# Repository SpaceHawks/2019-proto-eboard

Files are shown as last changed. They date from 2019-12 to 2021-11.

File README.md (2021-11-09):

This repository contains the schematic and PCB for the 2019-2020 electrical board. For a walkthrough of this season's progress and an in-depth explanation of the system, see the IPRO report. For a quick glance at the schematic or boards, look in the [PDFs](/PDFs) folder. For information not printed on the schematic (e.g. datasheet links, trace widths), open the files in KiCad.

To view or edit these files, use KiCad version 5. You may need to [install the latest libraries](http://kicad.org/libraries/download/) if they don't come with your installation.

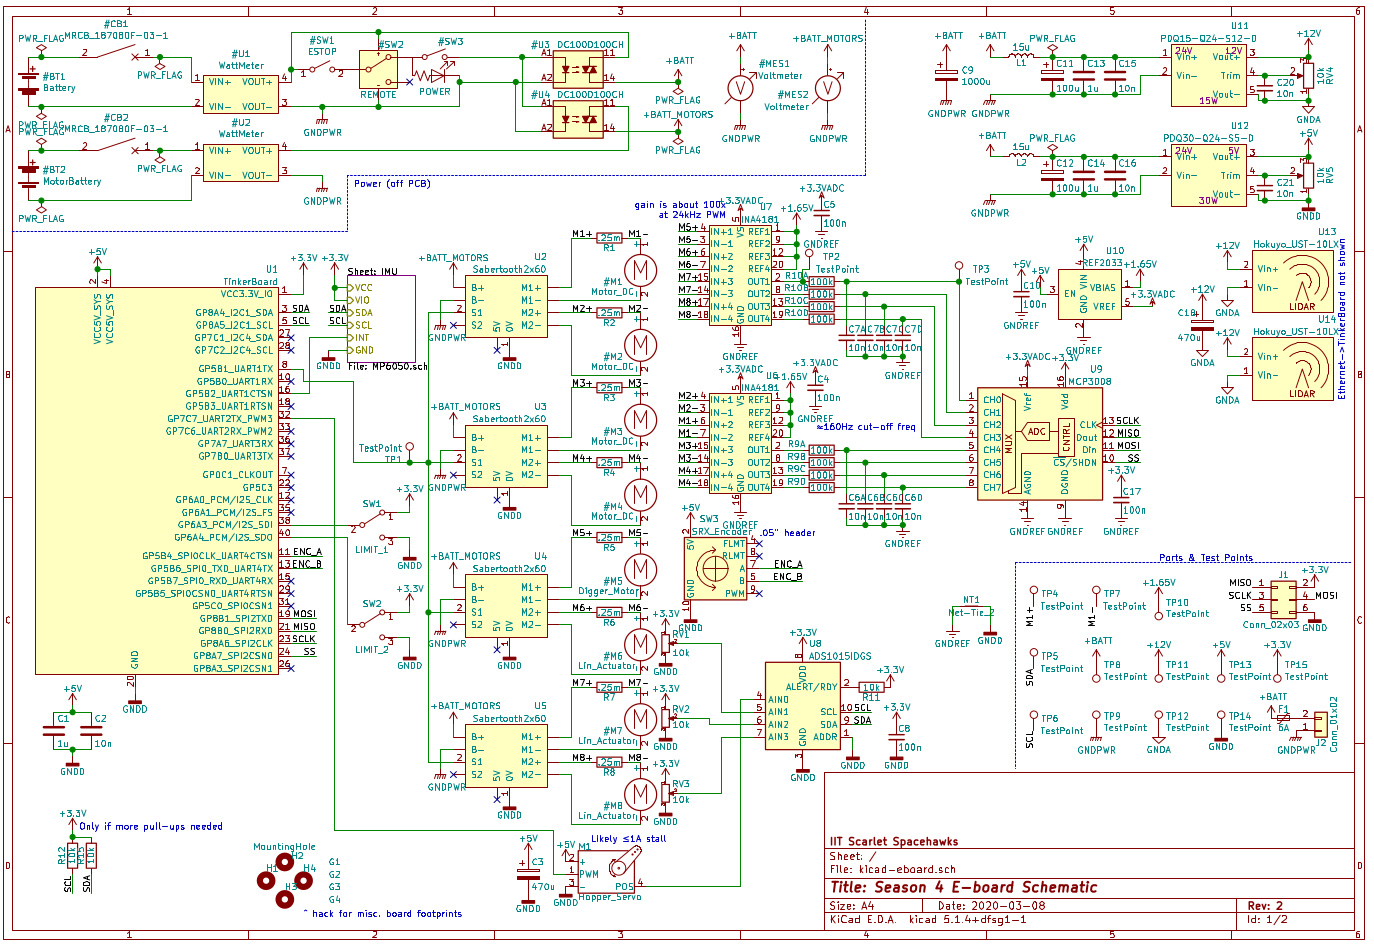
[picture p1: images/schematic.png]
Page 1 of the schematic (pretty much everything). See PDFs folder for something easier to read. The main schematic


# Spring 2020: Electrical Team IPRO Report

Gabriel Krell

Gregory Bonnema

Jack Pio

## I. Electrical Team Goals

The NASA RMC at Illinois Tech electrical team's goal was a reliable, professional electrical system for our robot. To accomplish this, we needed to plan the system in a reasonable, realistic way, implement our plan with well-reviewed eCAD, and turn those schematics into a physical robot. This year the team wanted to keep the same topology as previous years, making incremental changes. We aimed to have capable microelectronics and robot control systems running on top of a safe and reliable power system. Our robot would need to adhere to minimum specifications set by the competition (e.g. “The robot should include an emergency stop”) and those set by our goal-planning activity (e.g. “The robot should move”). We also had a nonfunctional goal: to spend as little as reasonably possible, designing to reuse parts from last year and use new parts we had already had. Overall our aim was to continue the success of the past NASA RMC teams, while improving efficiency and overall performance, making it easier to work together with the other subteams.

## II. Power Electronics

Conceptually, we split the electrical design of the robot into two sections. The “power electronics” section was chiefly concerned with getting power from batteries to motors in a safe way.

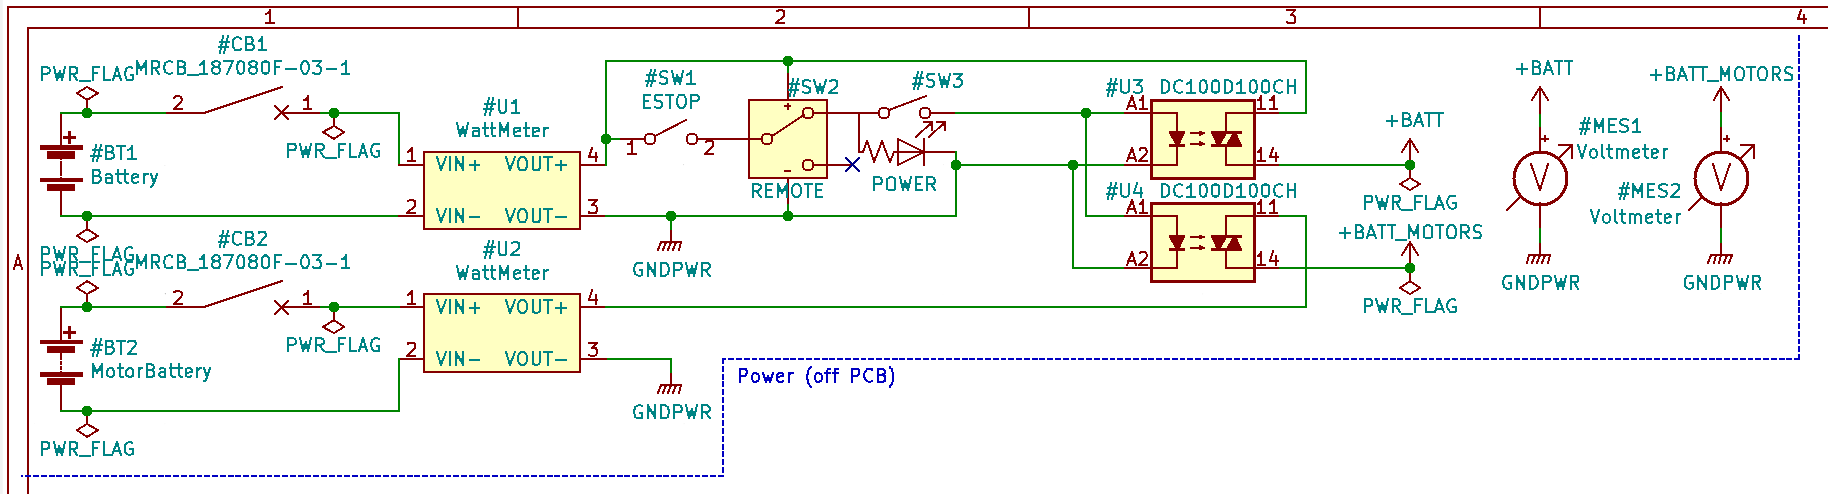
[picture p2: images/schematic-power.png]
The top-left corner of the schematic, labeled "Power (off PCB)" The power section of our final circuit schematic


### A. Initial Design

To lay out our plan for the power electronics section (and eventually make our final schematic), we started from a base of the previous year’s layout. Like other robotics competitions, the rules required an easy-to-reach emergency stop button (“E-stop”). We were also required to measure and display the total power consumed by the robot. On top of these mandatory elements, the relevant section of last year’s robot included:

- A single 3S hobby LiPo battery to power the robot

- A resettable circuit breaker to protect against sustained overcurrent

- A “remote E-stop” (actually a remote-controlled relay unit)

- A smaller, light-up power switch

- A solid-state relay (SSR) to toggle power to the robot

- Sabertooth 2x60 motor controllers to actually move the motors

- A panel-mount battery voltage display

We thought that this layout was simple to implement and was reasonably safe. We were able to build it using only parts that we already possessed from last year’s competition. However, we were concerned that the circuit breaker would take too long to open (10-25 seconds) during a projected overcurrent condition or short circuit. We investigated several options for faster responses: active control with a MOSFET, fast-blow fuses, and different circuit breakers. Unfortunately, breakers or fuses with our desired response characteristics were prohibitively expensive, and our subteam didn’t have the resources to implement active current protection. Ultimately, we compromised by including additional protection for the delicate microelectronics and trusting in the builtin current limiting on individual Sabertooths. Of course, we want to prevent any possible damage to the robot, but since this system includes a working E-stop and does not pose a fire hazard, it meets the relevant safety requirements.

### B. Modifications

We assembled a prototype electrical board as a proof-of-concept and began testing. We found that when motors were stalled, the high current draw would result in significant voltage drops across wires and especially across the SSR. This lowered the available voltage to below that required by the 12V-5V DC-DC converter, resulting in brownouts. We added a second SSR so that the microelectronics would not be affected by the high voltage drop across the SSR. We soon realized, however, that the high current was also causing the battery’s voltage to sag to unacceptable levels. To fix the problem, we added a second battery that would not be responsible for providing high current to the motors. This is not a perfect solution, because it required additional parts and weight, but it would perform well with the supplies on hand.

### C. Motor control

Like last year, we used Sabertooth 2x60 motor controllers. Each channel can supply up to 60A continuous or 120A peak; the Sabertooths are controlled via analog input, an R/C receiver, or serial input. Unfortunately, the controllers return no information about motor output or power consumption. To implement closed-loop control, we added output sensing for all motors: circuits to read the built-in potentiometers on the linear actuators, current sensing resistors on all motors, and a rotary encoder on the most critical motor.

## III. Microelectronics

The second section of the robot’s electronics system was responsible for sensor inputs, computation, and output signals. From the outset, we planned to use a PCB for reliable functionality in a small form factor.

The robot would be run by a single-board computer (SBC). The SBC would sense the outside world through an IMU and two LIDAR sensors, monitor the robot with current and position sensors, and output commands to the motor controllers. We initially used an ASUS Tinker Board, which we exchanged for a more powerful Raspberry Pi 3B+ at the request of the Programming Department.

### A. IMU

We included an inertial measurement unit (IMU) that would report the robot’s velocity and position in space. Because we already had a breakout board from Sparkfun, and because good libraries are available for it, we chose the MPU-6050 for our IMU. The MPU-6050 communicates with the SBC via I2C, a relatively slow multi-device protocol which is easy to connect and route on a circuit board. Sparkfun publishes schematics and board files for their hardware, so we included both the MPU-6050 circuit and headers to connect to the breakout. This way, we could use the expensive breakout board in our first PCB, but use the bare chip if a second version of the PCB forced us to order components.

### B. Potentiometer ADC

The robot incorporates three linear actuators and a four-wire servo to move the regolith collection system and sense how much icy regolith has been collected. All three linear actuators and the servo have built-in potentiometers for position sensing. Because our SBC was not able to read analog inputs by itself, we included an ADC to measure these voltages. We chose the ADS1015, an inexpensive 12-bit ADC that connects to the same I2C bus already used for the IMU. Adafruit sells an ADS1015 breakout board commonly used as an ADC for Raspberry Pis, so the Programming team would enjoy easy-to-use libraries to interface with the chip. Throughout the component selection process, we worked closely with Programming to make sure they would have drivers and libraries to interface with the hardware we chose.

### C. Current Sensing

After struggling with brownouts caused by excessive power consumption by the motors, we became concerned with monitoring motor current. The competition scoring penalized high power usage, but not enough for points to be our motivation. Rather, we wanted the robot to be able to detect when a motor was stalled (high current) or disconnected (no current despite a command to move). This would allow us to prevent system instability caused by current spikes, to improve navigation with this extra information about the robot’s movement, and to increase our eventual competition score.

We measured the voltage across very small (.25mΩ) shunt resistors to calculate the current going through each motor. Two leads from each resistor went to a differential current sense amplifier, which amplified the small bipolar voltage difference into a unipolar voltage high enough to be accurately measured by a fast ADC.

This was probably the most technically difficult part of the project. As the motors spin forwards or backwards, the motor controllers output 12V/0V or 0V/12V on the two leads (referenced to the negative lead of the battery). This means that a shunt resistor on either side will sometimes be at 12V potential, so a “high-side” current measurement system is necessary. Typical ADCs are damaged by inputs higher than their supply voltage (usually 3.3V or 5V), so we had to use a specialized IC to make a high-side differential measurement.

We also needed to amplify this measurement. To avoid large power losses in the resistors, we needed to keep the voltage drop across them as low as possible. To limit resistor consumption to 1W at the max motor current of 60A, we could only allow a voltage drop of 15mV. An ADC’s resolution is evenly distributed over its entire input range, so a 12-bit 3.3V ADC would only have 18 values to choose from to represent current of 0-60A. Amplifying this value before it went into the ADC allowed us to have more precise current measurements.

Finally, we needed to filter the amplified output of the differential measurement. The Sabertooth 2x60 modulates motor power with PWM at 24kHz. The ADC we chose had a maximum sample rate of 75k sps across all 8 channels, well below the Nyquist rate of the signal. Even if we were using a faster ADC, we didn’t want our software to process 384,000 samples per second, which would consume valuable system resources. Instead, we used an RC filter with a cut-off frequency of around 160Hz. This would smooth high-frequency PWM while giving us an accurate picture of changes in motor current. We considered using a Butterworth-response Sallen-Key filter, which has a much sharper cutoff of high frequencies and is easy to implement. But because we needed eight of these filters in limited board space and budget, we went with the RC filter.

## IV. Implementation

Implementation of our design was split into three parts: schematic capture, PCB design, and physical layout of large parts on the robot. We used KiCad for all our eCAD, and tracked versions with GitHub so that everyone was able to see the most up-to-date files.

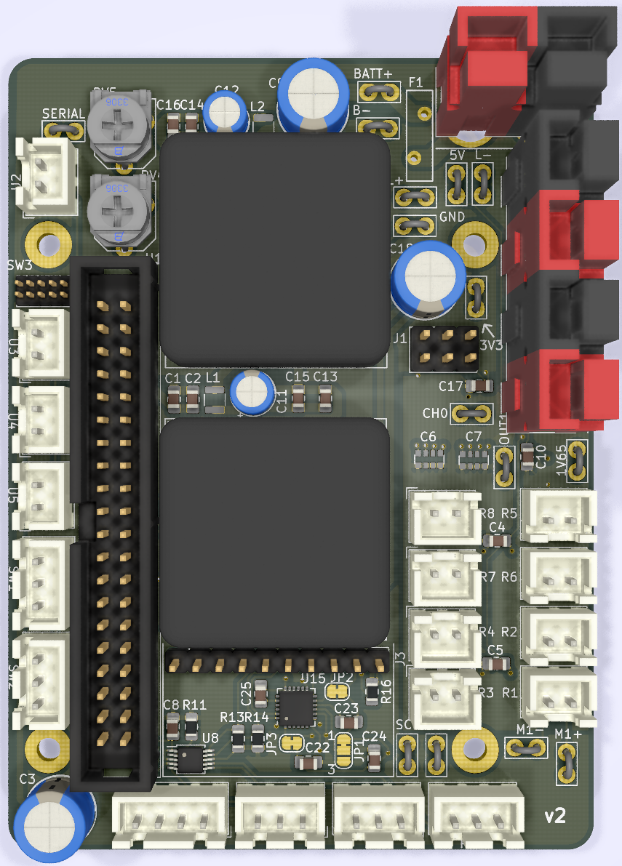
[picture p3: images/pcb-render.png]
A render of the final PCB
 The unpopulated PCB attached to a Tinker Board SBC

### A. Schematic

We began with a rough schematic focusing on the power electronics. We updated the schematic as we figured out how last year’s robot worked and made our own design changes. Having a reference design helped us quickly build the electrical system for a prototype robot, allowing us to verify the design and let Programming test out their code on real hardware. The prototype bot was invaluable for debugging the brownout problems mentioned in Section II-C. Work on the physical prototype and the schematic proceeded in tandem. Once we had implemented the microelectronics section on perfboard and verified motor control functionality, we were ready to design the PCB. At the same time, we knew that our well-tested power electronics section was unlikely to change, so we began planning the physical layout of the large parts on our robot.

### B. PCB

The PCB was designed over the course of several weeks, with an eye towards a small form factor and easy testability. To save space, we designed the board to stack on top of the SBC, and we included test points for the inevitable debugging sessions later on. After an initial online review, we ordered and tested the first version of the board. This version correctly supported motor control and the IMU, but we quickly realized that unlike the previous year’s Arduino, the Tinker Board does not have a built-in ADC. We had connected the built-in potentiometers of the linear actuators to GPIO pins that could only accept digital input. Luckily, we had scheduled plenty of time for a possible second PCB. We added the necessary ADC, along with some quality-of-life changes and the current sensing detailed in III-C, and ordered a second board.

### C. Physical Layout

With the designs of the PCB and schematic finalized, all that remained was the problem of how to apply these designs onto the robot itself. Given the extremely fine dust present in the competition, we decided to enclose the electrical system in a polycarbonate “e-box”. Our design was sealed with silicone caulk and included a removable front panel which slid on a set of rails. Although not entirely airtight, the box was designed to protect components from major dust contamination. We used weather-resistant panel-mount ports to connect the e-box with the motors, sensors, and emergency stop located elsewhere on the robot.

Our available space was scarcely larger than the total volume of the components, so we made careful mockups of different layouts to come up with a good arrangement. To save space, we stacked pairs of motor controllers, and stacked the PCB on top of the Tinker Board. The rest of the e-box was laid out around these core components, keeping in mind the aforementioned consideration for difficulty of wiring.

## VI. Conclusion

Although this year’s competition was interrupted by the COVID-19 pandemic, we still accomplished many of our goals for the robot and laid a strong foundation for next year. We also explored several promising areas for innovation in next year’s competition.

We designed and implemented a working, safe power system for the robot. We were able to identify historical trouble spots: the datasheet for the SSRs specified a large heat sink, and no heat sink had ever been used. This year, we used advanced phase change composite (PCC) heat sinks donated by AllCell, a local battery manufacturer. The lightweight phase change material absorbs energy as it melts, but is held together by a graphite substrate. This improves the performance and lifetime of the SSRs without adding a prohibitive amount of weight to the robot.

We are also proud of our microelectronics system. Rigorous online review and a schedule that allowed us time for a second spin produced a high-quality board. We were able to catch small issues: for instance, our second version of the board added rounded edges, optional pull-up resistors, and connectors that make it impossible to accidentally connect electrically-incompatible components. The removal of extraneous parts and overall simplification of the system allowed us to make a much more compact system than previous years.

We also accomplished our goal of minimal spending. Historically, the Electrical department has been responsible for a significant portion of the team’s budget. Last year, we spent $3,075 on parts and tools. This year, we spent $410, $232 of which went to soldering stations (the team possessed a single pencil-style iron with a damaged tip). Throughout the season, we designed with price in mind, using cheap or already-owned components.

As of this report, the pandemic has prevented us from receiving components to assemble the PCB, but we are hopeful that the parts will arrive so we can assemble the board and allow Programming to remotely test their software. We are confident in this year’s design, and hope it to be a great stepping stone to the future of the Scarlet Spacehawks.

## VII. Resources

[Don’t Fear the Filter: Lowpass Edition - Elliot Williams for Hackaday](https://hackaday.com/2017/03/08/dont-fear-the-filter-lowpass-edition/)

[Filter Design in Thirty Seconds - Bruce Carter for TI](http://www.ti.com/lit/an/sloa093/sloa093.pdf)

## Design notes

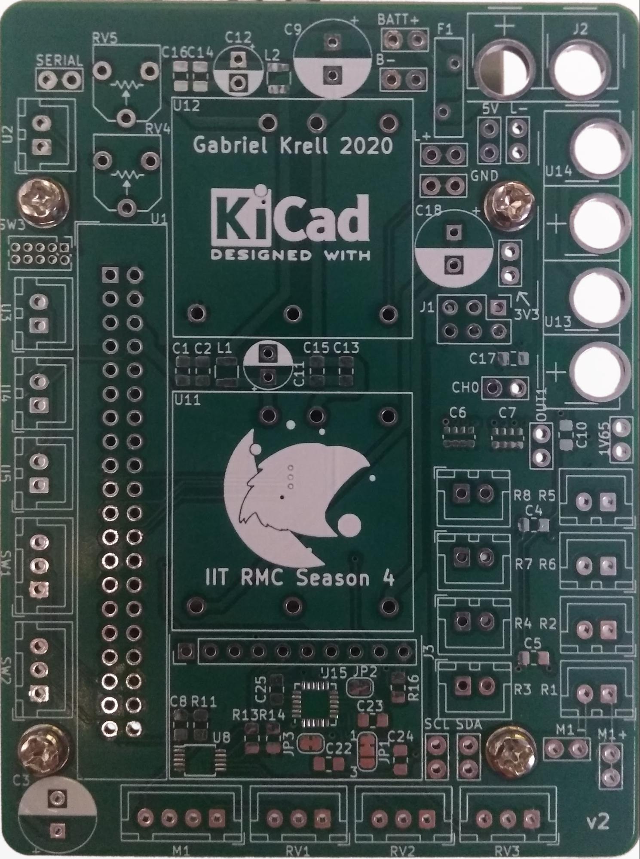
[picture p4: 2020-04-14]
images/pcb-unpopulated.jpg

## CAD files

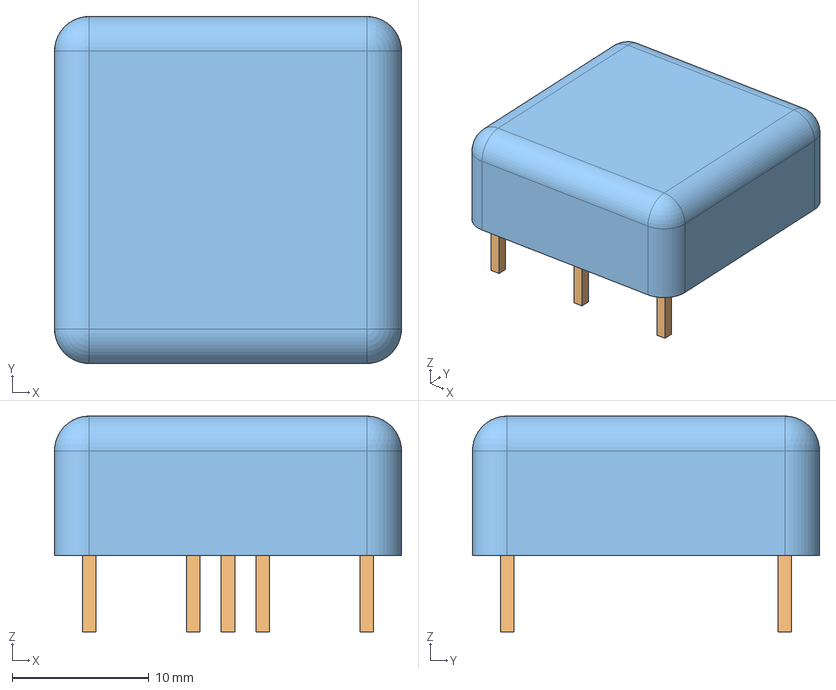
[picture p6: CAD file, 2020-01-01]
PDQ15.FCStd
25.4 x 25.4 x 15.8 mm
BottomPlastic
Pins
TopPlastic

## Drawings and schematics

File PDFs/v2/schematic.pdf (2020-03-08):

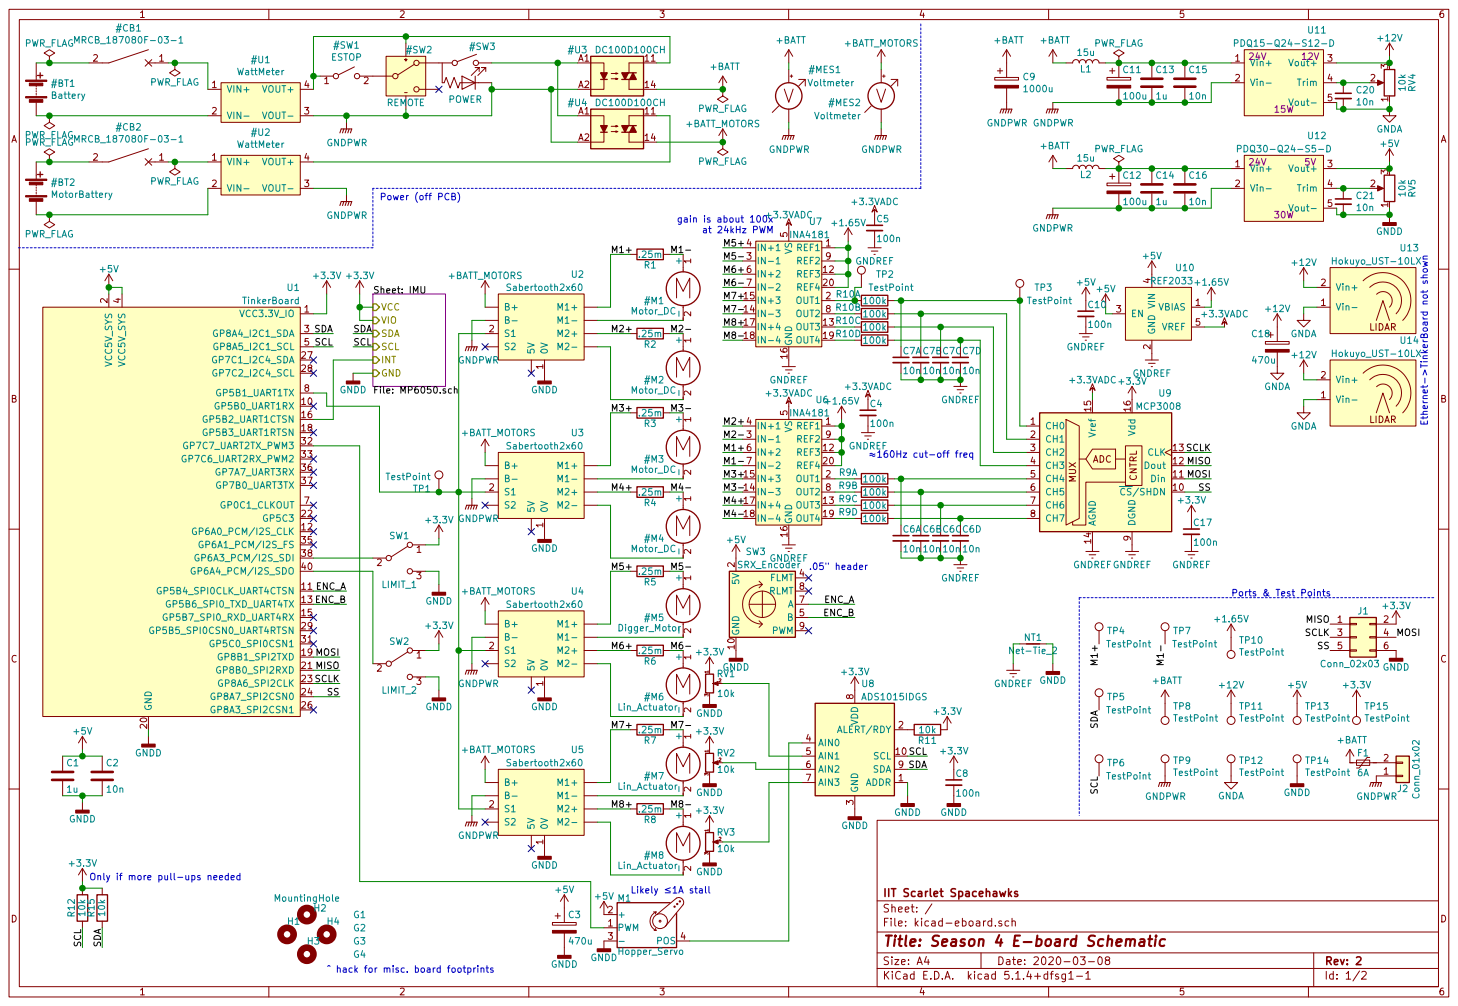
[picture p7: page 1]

Sheet: IMU
File: MP6050.sch VCC GND
VIO
INT SCL SDA

.05" header ^ hack for misc. board footprints

IIT Scarlet Spacehawks
File: kicad-eboard.sch Sheet: /
Id: 1/2 Title: Season 4 E-board Schematic

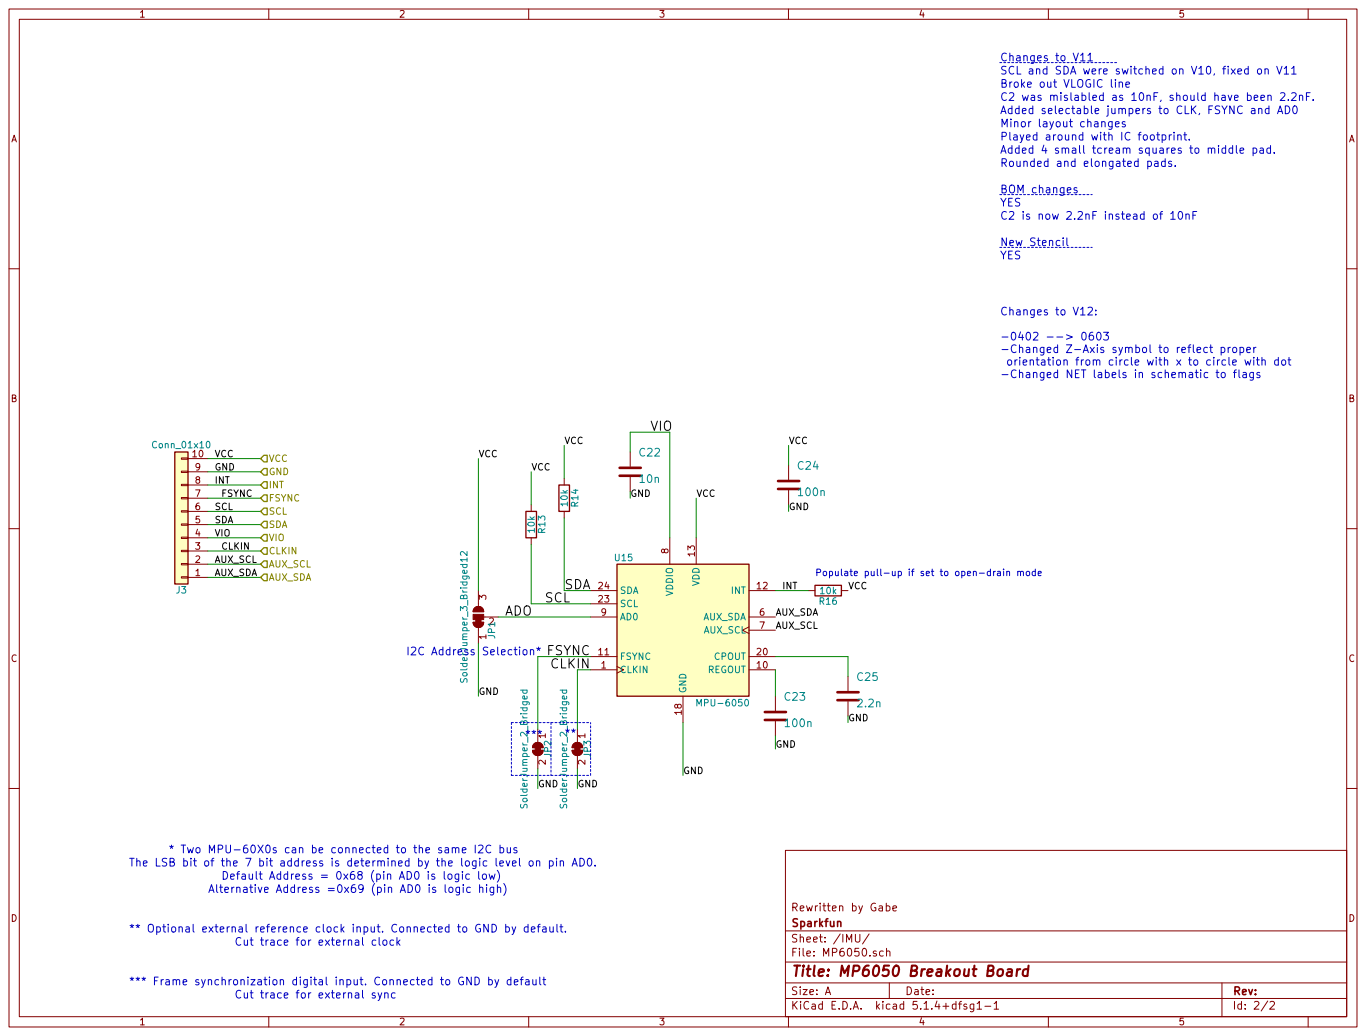
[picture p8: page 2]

Changes to V11
SCL and SDA were switched on V10, fixed on V11
C2 was mislabled as 10nF, should have been 2.2nF. Broke out VLOGIC line BOM changes

Added selectable jumpers to CLK, FSYNC and AD0
YES C2 is now 2.2nF instead of 10nF Minor layout changes
Played around with IC footprint.
Added 4 small tcream squares to middle pad.
Rounded and elongated pads.

-Changed Z-Axis symbol to reflect proper
orientation from circle with x to circle with dot -Changed NET labels in schematic to flags

Populate pull-up if set to open-drain mode

* Two MPU-60X0s can be connected to the same I2C bus

The LSB bit of the 7 bit address is determined by the logic level on pin AD0.

Alternative Address =0x69 (pin AD0 is logic high)

Rewritten by Gabe
File: MP6050.sch Sheet: /IMU/ Sparkfun

*** Frame synchronization digital input. Connected to GND by default

Id: 2/2 Title: MP6050 Breakout Board

Cut trace for external sync

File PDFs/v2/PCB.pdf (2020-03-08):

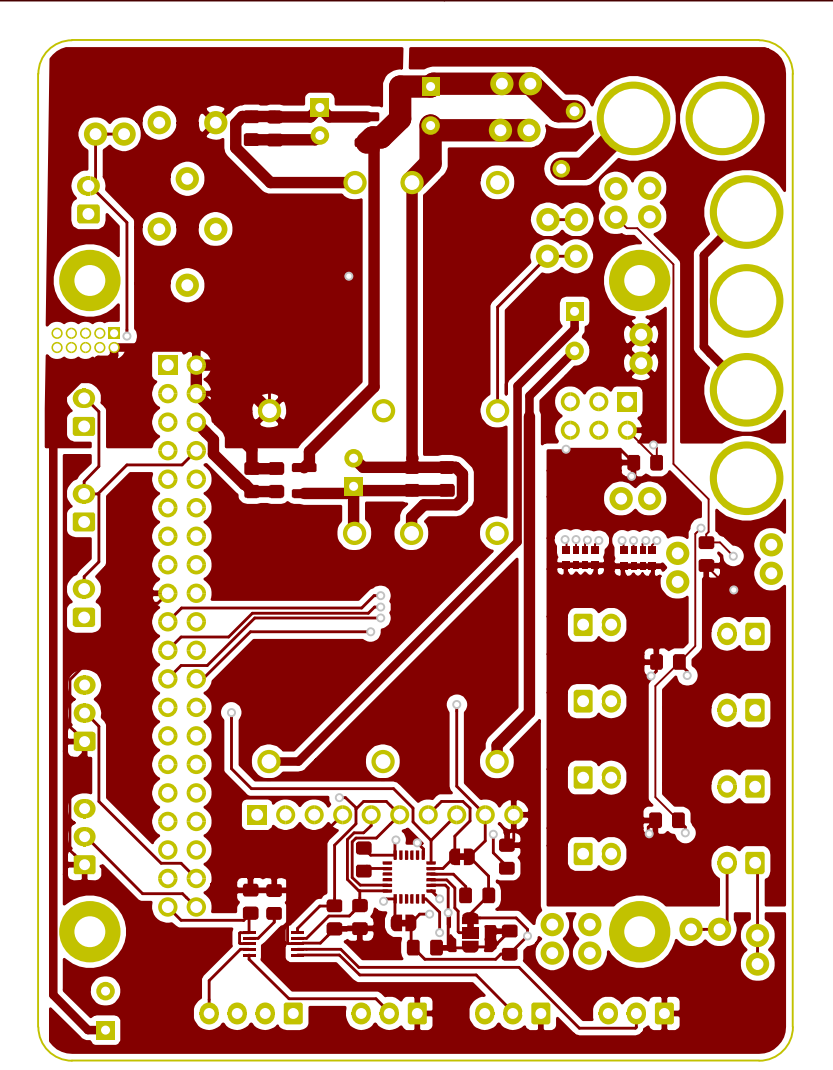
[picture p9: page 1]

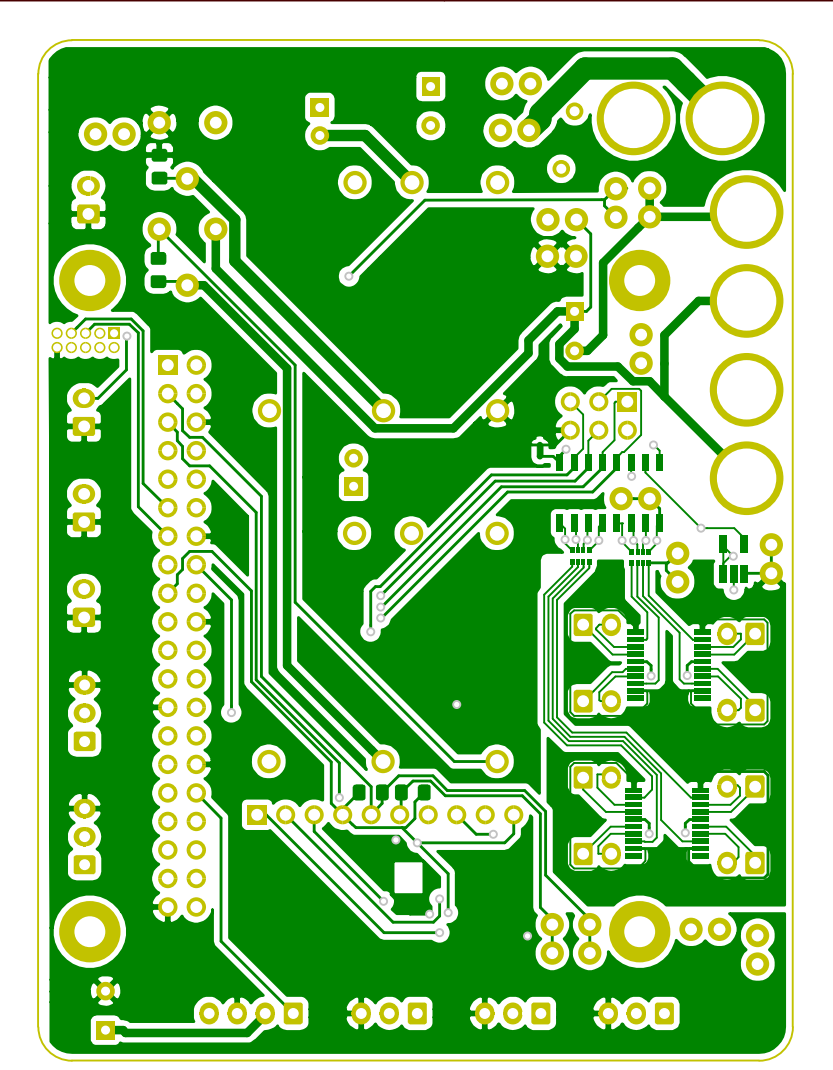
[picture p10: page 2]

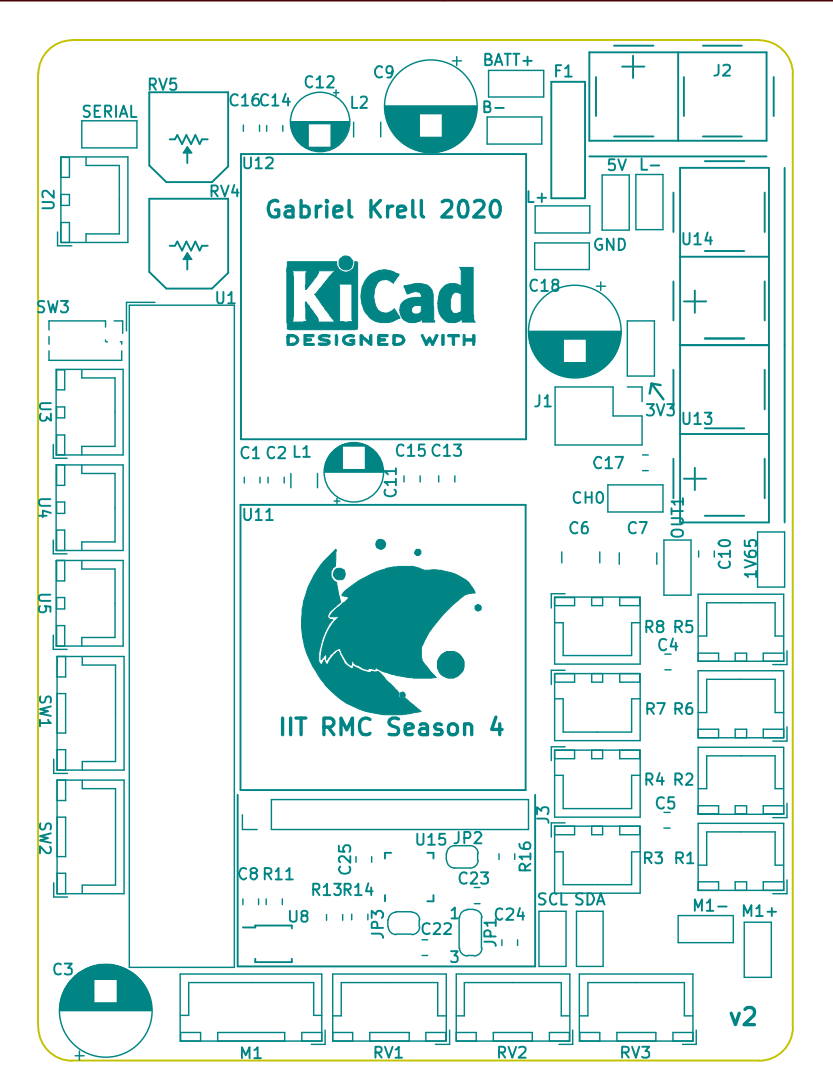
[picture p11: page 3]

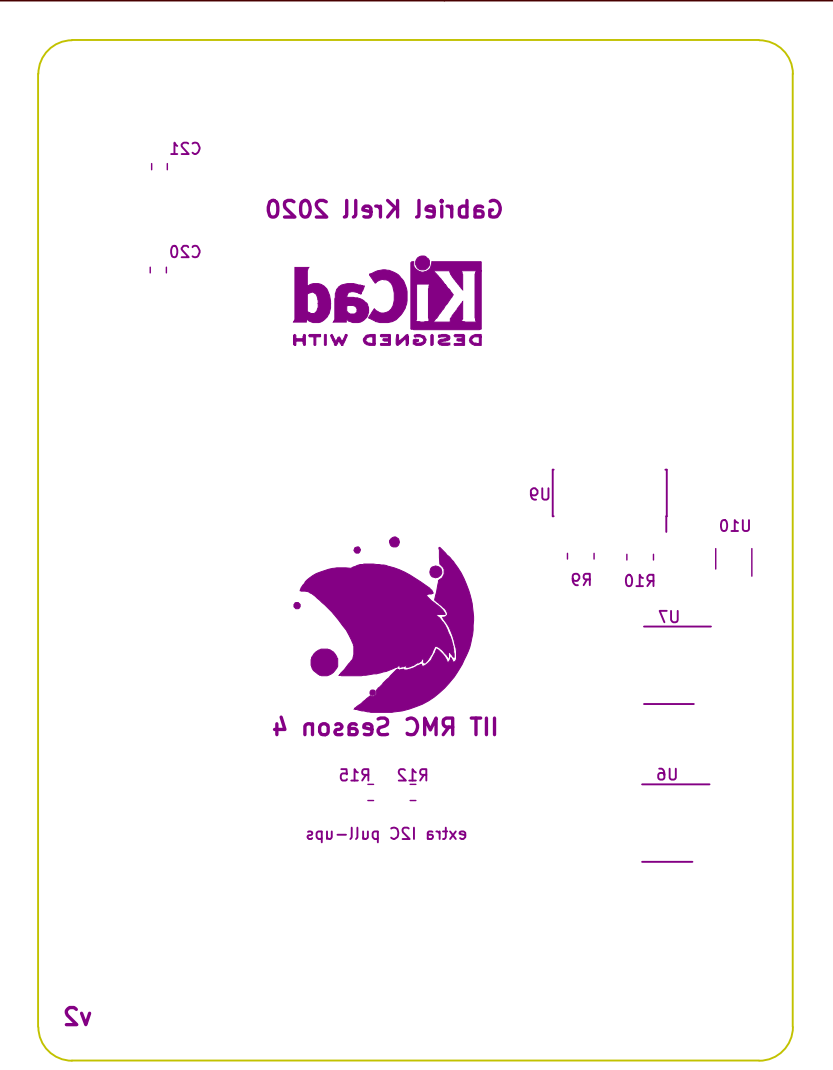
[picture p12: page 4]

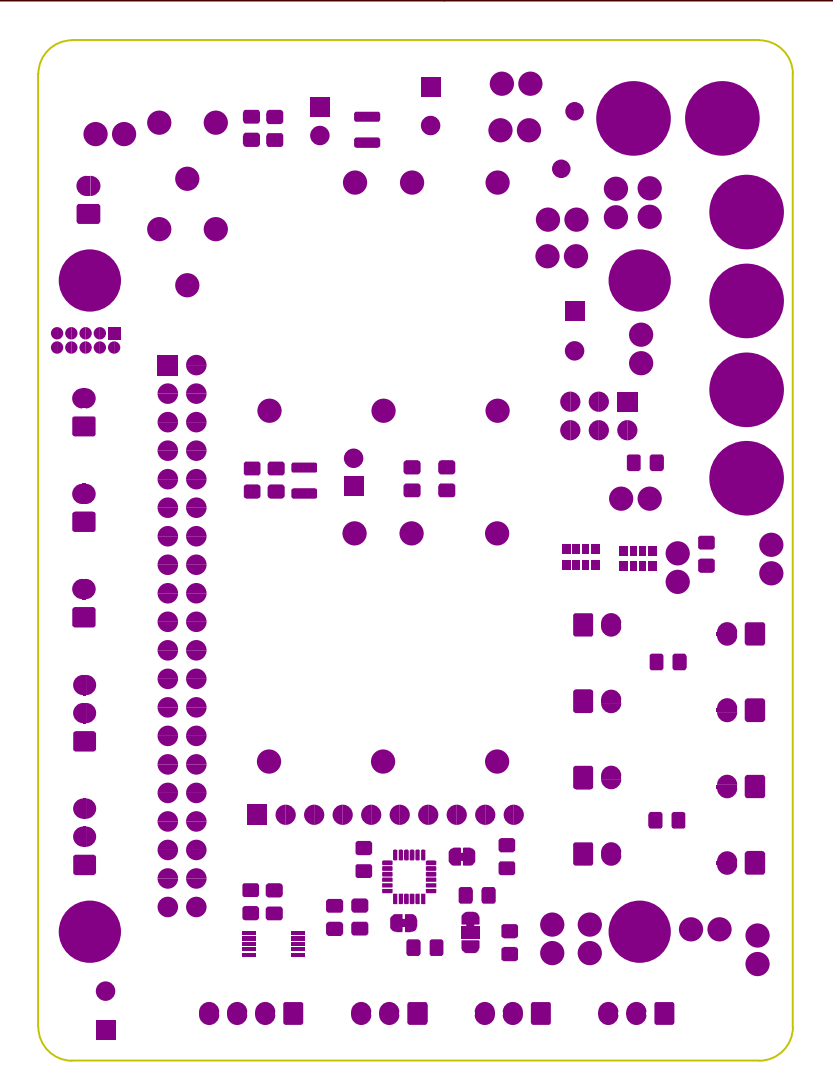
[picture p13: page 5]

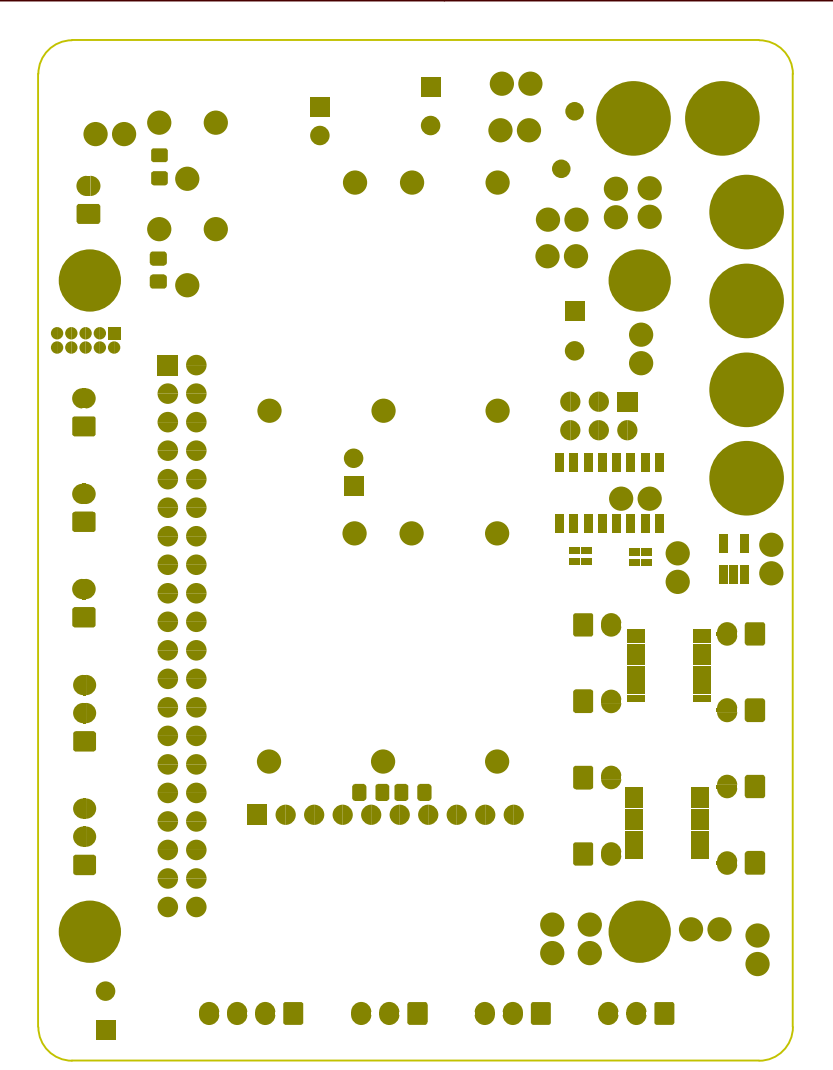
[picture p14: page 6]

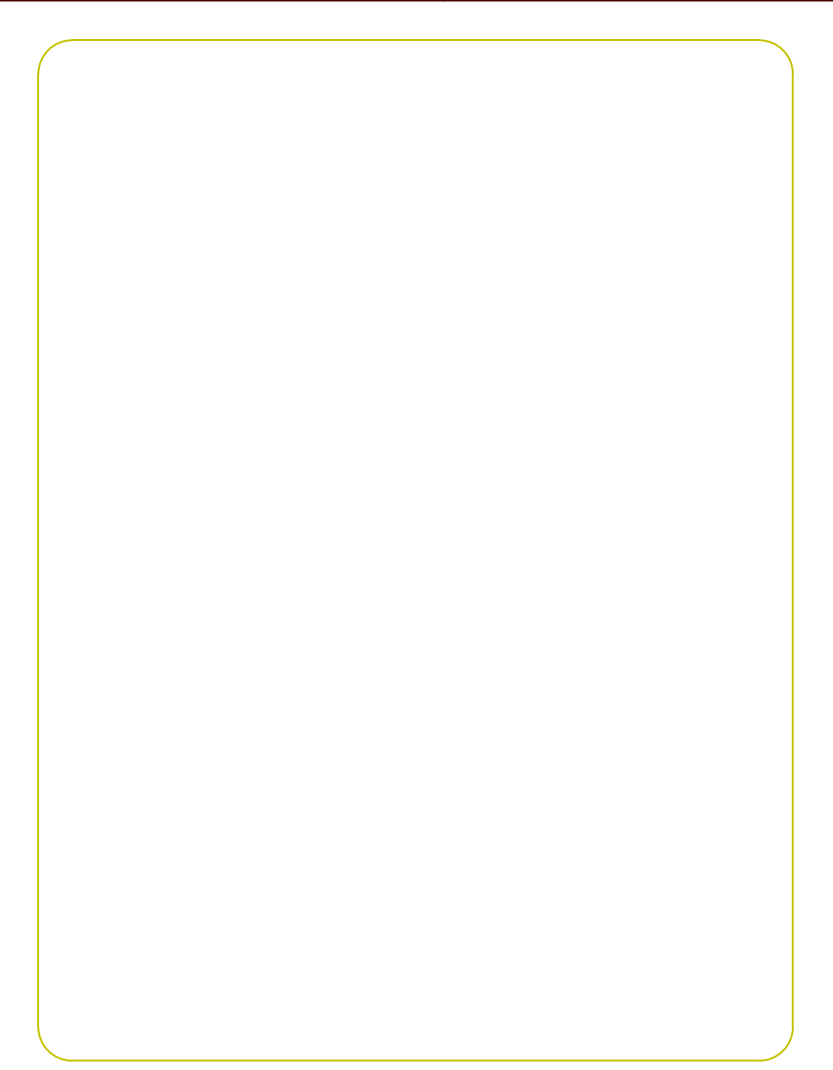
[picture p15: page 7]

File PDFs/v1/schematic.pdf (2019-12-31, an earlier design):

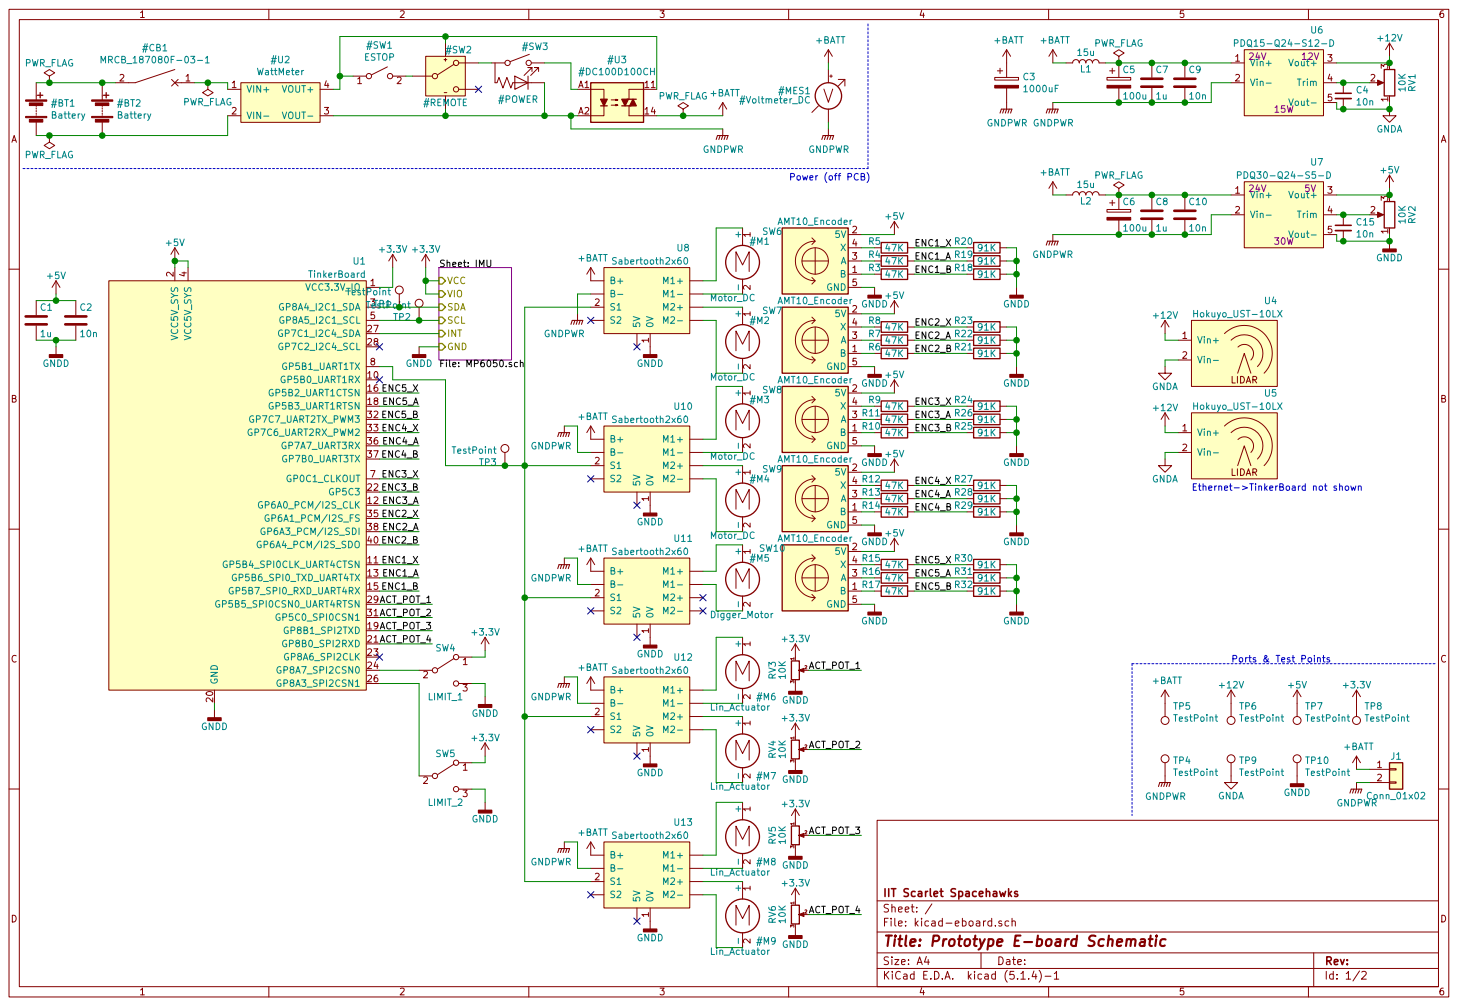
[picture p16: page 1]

Sheet: IMU
File: MP6050.sch VCC GND
VIO
INT SCL SDA

3 X | ENC2_A

1 | ENC2_B

3 X | ENC4_A

1 | ENC4_B

IIT Scarlet Spacehawks
File: kicad-eboard.sch Sheet: /
Id: 1/2 Title: Prototype E-board Schematic

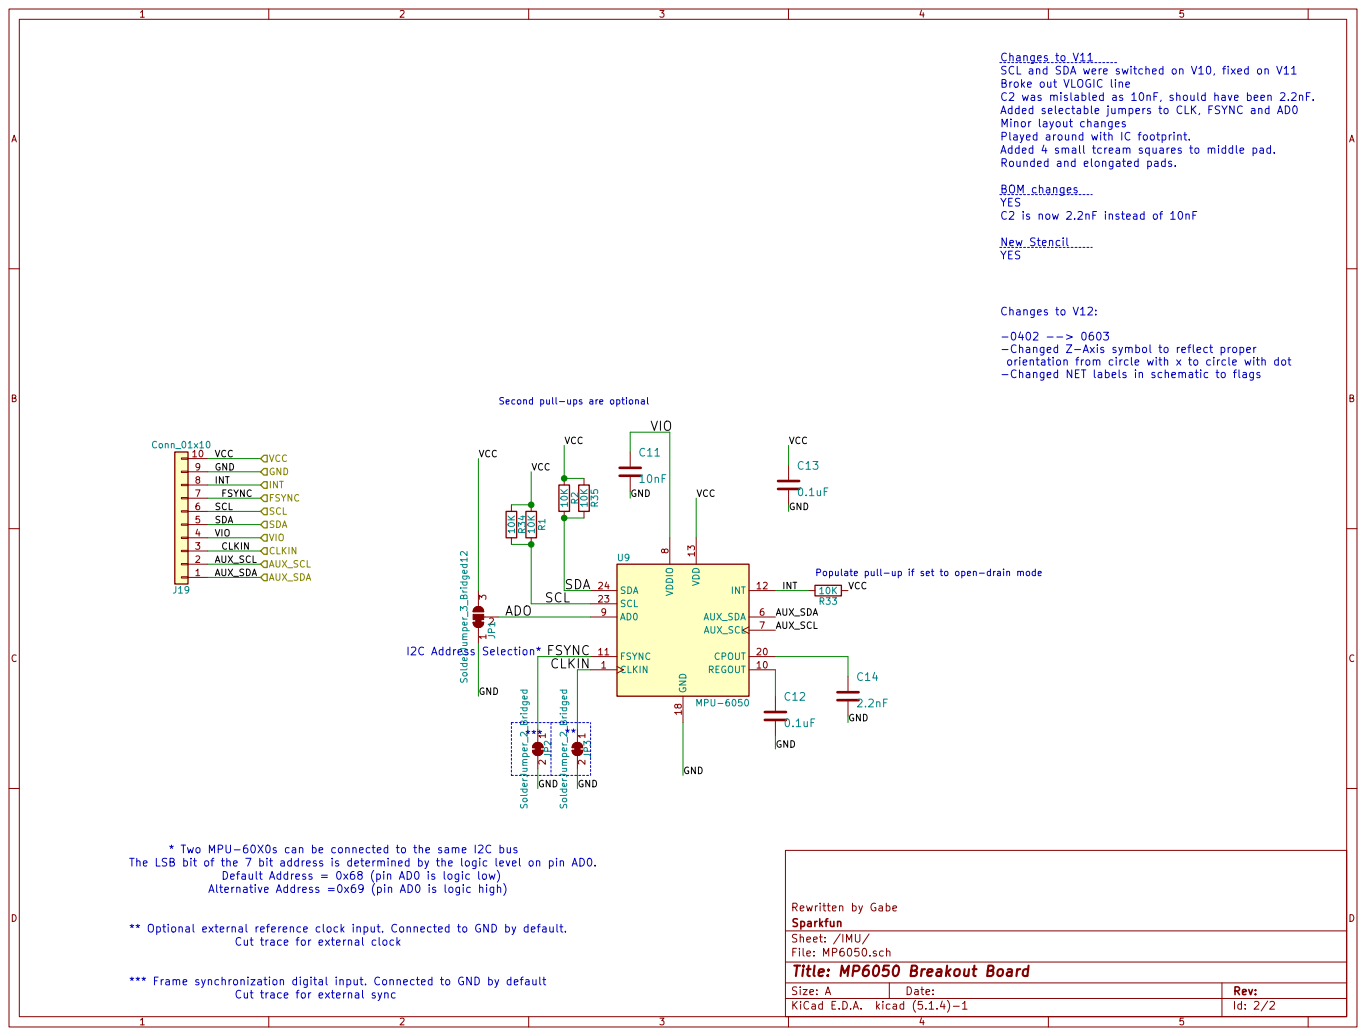
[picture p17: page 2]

Changes to V11
SCL and SDA were switched on V10, fixed on V11

C2 was mislabled as 10nF, should have been 2.2nF.
Added selectable jumpers to CLK, FSYNC and AD0

Played around with IC footprint.
Added 4 small tcream squares to middle pad.

BOM changes New Stencil YES
YES

-Changed Z-Axis symbol to reflect proper
orientation from circle with x to circle with dot -Changed NET labels in schematic to flags

Second pull-ups are optional

** Default Address = 0x68 (pin AD0 is logic low)

Cut trace for external sync * Two MPU-60X0s can be connected to the same I2C bus

File: MP6050.sch Sheet: /IMU/ Sparkfun

** Optional external reference clock input. Connected to GND by default. Cut trace for external clock

*** Frame synchronization digital input. Connected to GND by default

Id: 2/2 Title: MP6050 Breakout Board

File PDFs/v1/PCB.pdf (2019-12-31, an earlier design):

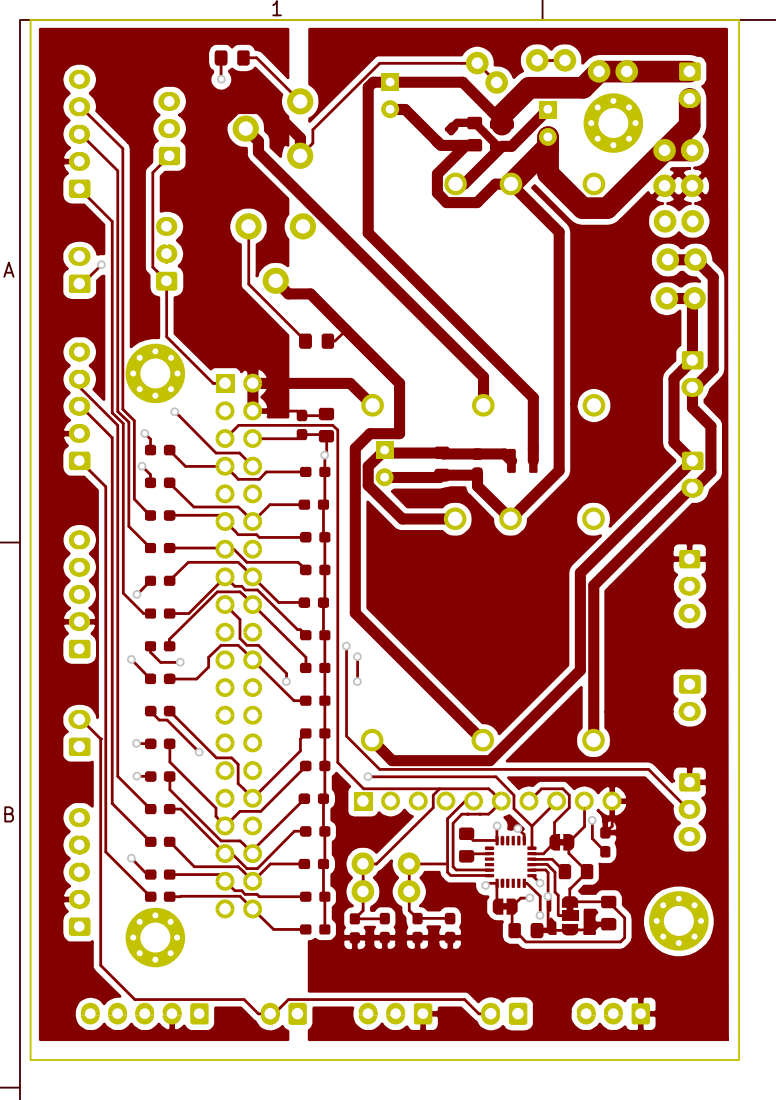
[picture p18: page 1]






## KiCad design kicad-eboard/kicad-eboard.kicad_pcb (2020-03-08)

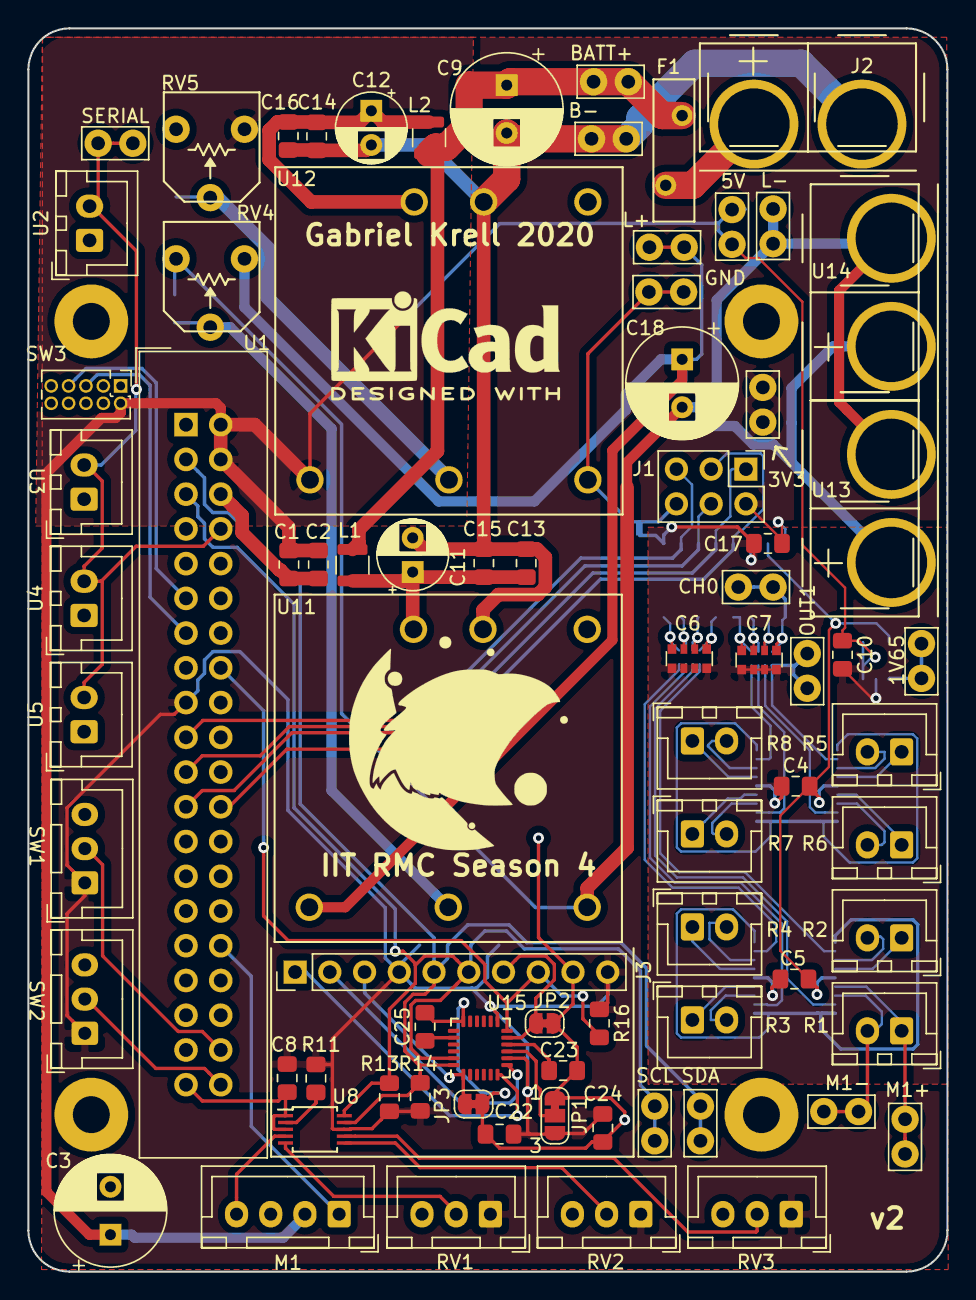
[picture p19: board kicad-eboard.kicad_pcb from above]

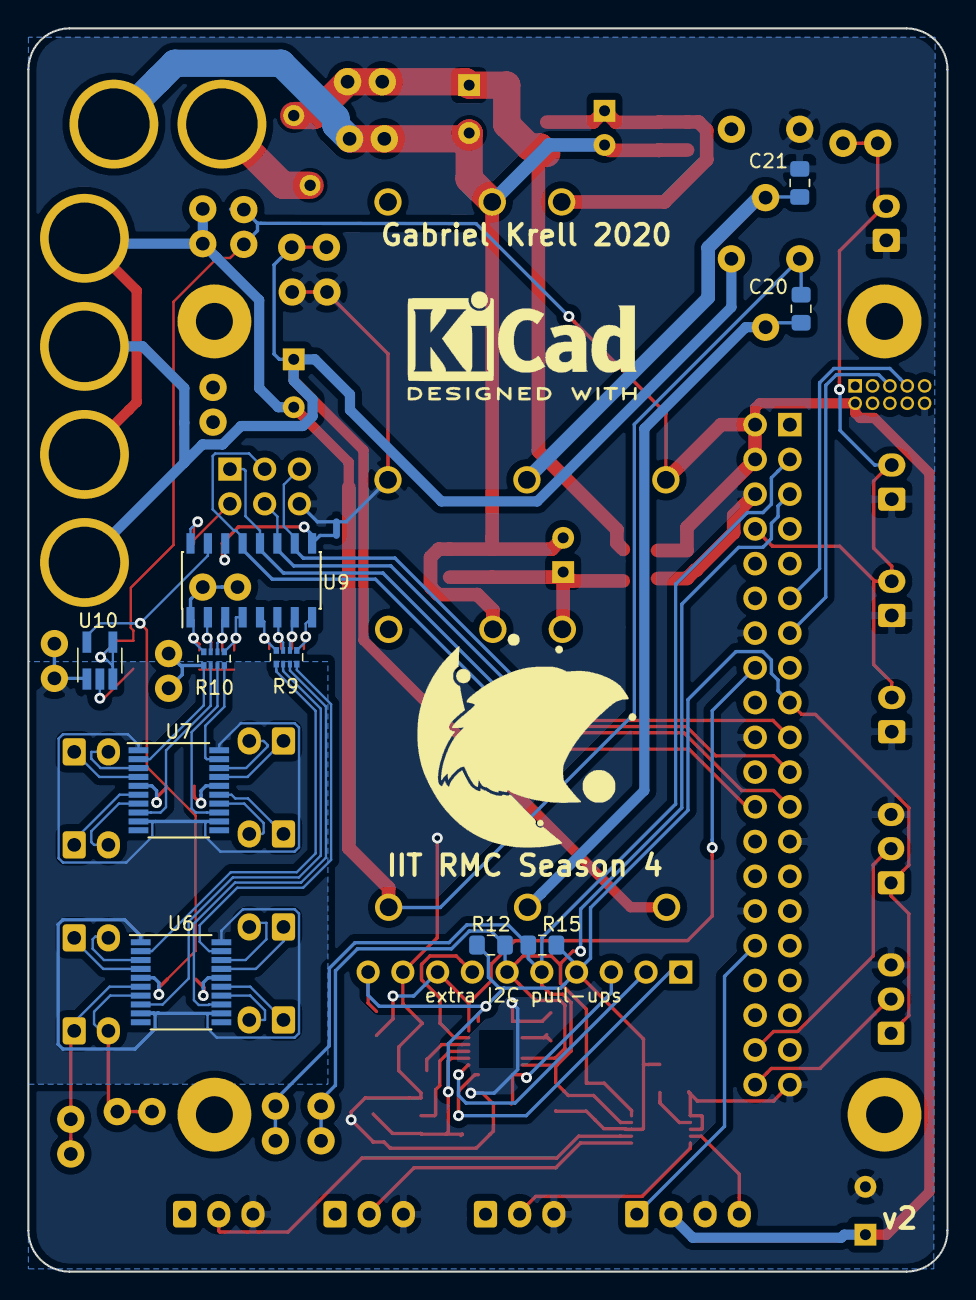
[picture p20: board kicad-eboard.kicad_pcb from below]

Board: 4 copper layers, 67.2 x 90.9 mm, 97 parts (13 on the bottom side), 72 nets.

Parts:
C1, C13, C14: 1u; C_0805_2012Metric_Pad1.15x1.40mm_HandSolder
C2, C15, C16, C20, C21, C22: 10n; C_0805_2012Metric_Pad1.15x1.40mm_HandSolder
C3, C18: 470u; CP_Radial_D8.0mm_P3.50mm
C4, C5, C8, C10, C17, C23, C24: 100n; C_0805_2012Metric_Pad1.15x1.40mm_HandSolder
C6, C7: 10n; C_Array_Convex_4x0612
C9: 1000u; CP_Radial_D8.0mm_P3.50mm
C11, C12: 100u; CP_Radial_D5.0mm_P2.50mm
C25: 2.2n; C_0805_2012Metric_Pad1.15x1.40mm_HandSolder
F1: 6A; Fuse_Littelfuse_16R600G
G1, G2: Logo; KiCad-Logo2_8mm_SilkScreen
G3, G4: Logo; SSH_logo
H1, H2, H3, H4: MountingHole; MountingHole_2.7mm_M2.5_Pad
J1: Conn_02x03; PinHeader_2x03_P2.54mm_Vertical
J2: Conn_01x02; Powerpole_45A_Vert_01x02_Holes
J3: Conn_01x10; PinHeader_1x10_P2.54mm_Vertical
JP1: SolderJumper_3_Bridged12; SolderJumper-3_P1.3mm_Bridged12_RoundedPad1.0x1.5mm_NumberL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
JP2, JP3: SolderJumper_2_Bridged; SolderJumper-2_P1.3mm_Bridged_RoundedPad1.0x1.5mm
L1, L2: 15u; L_1008_2520Metric
M1: Hopper_Servo; JST_XH_B4B-XH-A_1x04_P2.50mm_Vertical
NT1: Net-Tie_2; NetTie-2_SMD_Pad0.5mm
R1, R2, R3, R4, R5, R6, R7, R8: .25m; JST_XH_B2B-XH-A_1x02_P2.50mm_Vertical
R9, R10: 100k; R_Array_Convex_4x0402
R11, R12, R13, R14, R15, R16: 10k; R_0805_2012Metric_Pad1.15x1.40mm_HandSolder
RV1, RV2, RV3: 10k; JST_XH_B3B-XH-A_1x03_P2.50mm_Vertical
RV4, RV5: 10k; Potentiometer_Bourns_3306F
SW1: LIMIT_1; JST_XH_B3B-XH-A_1x03_P2.50mm_Vertical
SW2: LIMIT_2; JST_XH_B3B-XH-A_1x03_P2.50mm_Vertical
SW3: SRX_Encoder; PinHeader_2x05_P1.27mm_Vertical
TP1, TP2, TP3, TP4, TP5, TP6, TP7, TP8, TP9, TP10, TP11, TP12, TP13, TP14, TP15: TestPoint; TestPoint_Bridge_Pitch2.54mm_Drill1.0mm
U1: TinkerBoard; IDC-Header_2x20_P2.54mm_Vertical
U2, U3, U4, U5: Sabertooth2x60; JST_XH_B2B-XH-A_1x02_P2.50mm_Vertical
U6, U7: INA4181; TSSOP-20_4.4x6.5mm_P0.65mm
U8: ADS1015IDGS; TSSOP-10_3x3mm_P0.5mm
U9: MCP3008; SOIC-16_3.9x9.9mm_P1.27mm
U10: REF2033; SOT-23-5_HandSoldering
U11: PDQ15-Q24-S12-D; PDQXX-D_DC-DC_converter
U12: PDQ30-Q24-S5-D; PDQXX-D_DC-DC_converter
U13, U14: Hokuyo_UST-10LX; Powerpole_45A_Vert_01x02_Holes
U15: MPU-6050; InvenSense_QFN-24_4x4mm_P0.5mm

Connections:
+1.65V: TP10.1, U6.1, U6.9, U6.12, U6.20, U7.1, U7.9, U7.12, U7.20, U10.1
+3.3VADC: C4.1, C5.1, U6.5, U7.5, U9.15, U10.5
+3V3: C8.1, C17.1, C22.1, C24.1, J1.2, J3.4, J3.10, JP1.3, R11.1, R12.2, R13.1, R14.1, R15.2, R16.1, RV1.1, RV2.1, RV3.1, SW1.1, SW2.1, TP15.1, U1.1, U1.17, U8.8, U9.16, U15.8, U15.13
+5V: C1.1, C2.1, C3.1, C10.1, M1.2, RV5.3, SW3.2, TP13.1, U1.2, U1.4, U10.3, U10.4, U12.3
+12V: C18.1, RV4.3, TP11.1, U11.3, U13.2, U14.2
+BATT: C9.1, F1.2, L1.1, L2.1, TP8.1
/ENC_A: SW3.7, U1.11
/ENC_B: SW3.5, U1.13
/IMU/ADO: JP1.2, U15.9
/IMU/AUX_SCL: J3.2, U15.7
/IMU/AUX_SDA: J3.1, U15.6
/IMU/CLKIN: J3.3, JP3.1, U15.1
/IMU/FSYNC: J3.7, JP2.1, U15.11
/IMU/INT: J3.8, R16.2, U1.16, U15.12
/M1+: R1.1, TP4.1, U6.6
/M1-: R1.2, TP7.1, U6.7
/M2+: R2.1, U6.4
/M2-: R2.2, U6.3
/M3+: R3.1, U6.15
/M3-: R3.2, U6.14
/M4+: R4.1, U6.17
/M4-: R4.2, U6.18
/M5+: R5.1, U7.4
/M5-: R5.2, U7.3
/M6+: R6.1, U7.6
/M6-: R6.2, U7.7
/M7+: R7.1, U7.15
/M7-: R7.2, U7.14
/M8+: R8.1, U7.17
/M8-: R8.2, U7.18
/MISO: J1.1, U1.21, U9.12
/MOSI: J1.4, U1.19, U9.11
/SCL: J3.6, R12.1, R13.2, TP6.1, U1.5, U8.10, U15.23
/SCLK: J1.3, U1.23, U9.13
/SDA: J3.5, R14.2, R15.1, TP5.1, U1.3, U8.9, U15.24
/SS: J1.5, U1.24, U9.10
GND: C1.2, C2.2, C3.2, C8.2, C21.2, C22.2, C23.2, C24.2, C25.2, J1.6, J3.9, JP1.1, JP2.2, JP3.2, M1.3, NT1.2, RV1.3, RV2.3, RV3.3, RV5.1, SW1.3, SW2.3, SW3.10, TP14.1, U1.6, U1.9, U1.14, U1.20, U1.25, U1.30, U1.34, U1.39, U2.1, U3.1, U4.1, U5.1, U8.1, U8.3, U12.5, U15.18
GNDA: C18.2, C20.2, RV4.1, TP12.1, U11.5, U13.1, U14.1
GNDPWR: C9.2, C11.2, C12.2, C13.2, C14.2, C15.2, C16.2, J2.1, TP9.1, U11.2, U12.2
GNDREF: C4.2, C5.2, C6.5, C6.6, C6.7, C6.8, C7.5, C7.6, C7.7, C7.8, C10.2, C17.2, NT1.1, U6.16, U7.16, U9.9, U9.14, U10.2
unnamed: C6.1, R9.8, U9.5
unnamed: C6.2, R9.7, U9.6
unnamed: C6.3, R9.6, U9.7
unnamed: C6.4, R9.5, U9.8
unnamed: C7.1, R10.8, TP3.1, U9.1
unnamed: C7.2, R10.7, U9.2
unnamed: C7.3, R10.6, U9.3
unnamed: C7.4, R10.5, U9.4
unnamed: C11.1, C13.1, C15.1, L1.2, U11.1
unnamed: C12.1, C14.1, C16.1, L2.2, U12.1
unnamed: C20.1, RV4.2, U11.4
unnamed: C21.1, RV5.2, U12.4
unnamed: C23.1, U15.10
unnamed: C25.1, U15.20
unnamed: F1.1, J2.2
unnamed: M1.1, U1.32
unnamed: M1.4, U8.4
unnamed: R9.1, U6.2
unnamed: R9.2, U6.8
unnamed: R9.3, U6.13
unnamed: R9.4, U6.19
unnamed: R10.1, TP2.1, U7.2
unnamed: R10.2, U7.8
unnamed: R10.3, U7.13
unnamed: R10.4, U7.19
unnamed: R11.2, U8.2
unnamed: RV1.2, U8.5
unnamed: RV2.2, U8.6
unnamed: RV3.2, U8.7
unnamed: SW1.2, U1.38
unnamed: SW2.2, U1.40
unnamed: TP1.1, U1.8, U2.2, U3.2, U4.2, U5.2

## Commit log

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2019-09-29 Add initial SSR section
    [kicad-eboard.sch]
2019-10-04 Add circuit breaker symbols
    These are taken from the Device library, but are a pain to use if your KiCad
    install doesn't come with the latest Device. Best practice is probably gonna
    be to copy in everything that's not like R, C, etc.
2019-10-04 Add PWM breakout board
    [I2CtoPWM.sch, kicad-eboard.sch]
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2019-10-04 Fill in some power topology
    [kicad-eboard.sch]
2019-10-04 Satisfy some ERC things
    [I2CtoPWM.sch, kicad-eboard.sch]
2019-10-04 Add input filtering, trim to DC-DCs
    [kicad-eboard.sch]
2019-10-04 Add TinkerBoard decoupling caps
    [kicad-eboard.sch]
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2019-10-04 Add IMU breakout board
    [I2CtoPWM.sch, MP6050.sch, kicad-eboard.sch]
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2019-10-05 6 sabertooths, 1 per motor, subsheets
    [I2CtoPWM.sch, MP6050.sch, MotorController.sch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]
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2019-10-07 Add encoders to schematic
    Add an encoder to each Sabertooth. Encoders can't run on 3.3V but 5V will
    damage TinkerBoard, so level shifter (voltage divider) is required. Just
    gave up and used air wires.
    Shifted over this section of main schematic to make room.
    [MP6050.sch, MotorController.sch, kicad-eboard.sch]
2019-10-07 Add limit switches; annotate
    [I2CtoPWM.sch, MP6050.sch, MotorController.sch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]
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2019-10-23 Add power to wireless relay, light-up switch
    [kicad-eboard.sch]
2019-10-30 Fix I2C->PWM power
    [I2CtoPWM.sch, MP6050.sch, MotorController.sch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]
2019-10-30 Two motors per Sabertooth; fix PWM inputs
    [I2CtoPWM.sch, MP6050.sch, MotorController.sch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]
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2019-10-30 MPU-6050 is 3V3, not 5V
    [kicad-eboard.sch]
2019-10-30 Scooch over battery ground
    [kicad-eboard.sch]
2019-10-30 Fix ERC errors (add some power flags)
    [MotorController.sch, kicad-eboard.sch]
2019-11-09 Use serial instead of analog Sabertooth ctrl
    [I2CtoPWM.sch, MP6050.sch, MotorController.sch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]
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2019-11-09 Add circuit breaker name, datasheet
    [kicad-eboard.sch]
2019-11-10 Tweak DCDC converter text position
    [kicad-eboard.sch]
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2019-11-10 Add weird Windows changes
    [MP6050.sch, kicad-eboard.sch]
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2019-11-10 Use 91k resistors instead of two 47k to fit parts on hand
    [kicad-eboard.sch]
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2019-11-10 Add footprints for DC-DC converters
    [kicad-eboard.sch]
2019-11-13 Add more test points, battary->PCB connector
    [MP6050.sch, kicad-eboard.sch]
2019-11-13 Move #s to actually work
    [MP6050.sch, kicad-eboard.sch]
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2019-11-13 Add initial PCB component placement
    [kicad-eboard.kicad_pcb]
2019-11-22 Fix footprint
    [kicad-eboard.sch]
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2019-11-24 Add emergency cap on 5V area; more routing
    [MP6050.sch, kicad-eboard.kicad_pcb, kicad-eboard.sch]
2019-12-24 Add breakout option for MP6050
    [kicad-eboard.kicad_pcb]
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2019-12-25 Fix inductor footprint
    [MP6050.sch, kicad-eboard.kicad_pcb, kicad-eboard.sch]
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2019-12-26 Finish arrangement, start routing
    [kicad-eboard.kicad_pcb, kicad-eboard.sch]
2019-12-27 Annotate mounting holes; rotate board to fit screen
    [kicad-eboard.kicad_pcb]
2019-12-27 Route first F.CU traces; reorder some inputs
    [kicad-eboard.kicad_pcb, kicad-eboard.sch]
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2019-12-27 Fix inductor broken by merge?
    [kicad-eboard.sch]
2019-12-27 Fix broken 3v3 pour
    [kicad-eboard.kicad_pcb]
2019-12-27 Add SSH logo; move vias to accomodate
    [kicad-eboard.kicad_pcb]
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2019-12-28 Add version number silkscreen
    [kicad-eboard.kicad_pcb]
2019-12-28 Add orientation symbol to pots
    [kicad-eboard.kicad_pcb, kicad-eboard.sch]
2019-12-28 Add readable test point silkscreens
    [kicad-eboard.kicad_pcb]
2019-12-28 Clean up perimeter silkscreen
    [kicad-eboard.kicad_pcb]
2019-12-28 Add INT pull-up
    I put this inside the MP6050 instead of outside the module where it "should" go
    because there wasn't really room in the schematic to put it on the first sheet.
    [MP6050.sch, kicad-eboard.kicad_pcb]
2019-12-29 Add emergency I2C resistors
    The sub-sheet has kind of fallen out of sync with the Sparkfun original; I
    probably should have put the new resistors on sheet 1
    [MP6050.sch, kicad-eboard.kicad_pcb]
2019-12-29 Add caps to trimpots
    [MP6050.sch, kicad-eboard.kicad_pcb, kicad-eboard.sch]
2019-12-29 Fix some DRC problems
    [MP6050.sch, kicad-eboard.kicad_pcb, kicad-eboard.sch]
2019-12-29 Move silkscreen off vias
    [kicad-eboard.kicad_pcb]
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2019-12-29 More fiddling for 4pcb
    [kicad-eboard.kicad_pcb]
2020-01-01 Add PDQXX 3D model
    [PDQ15.FCStd, kicad-eboard.kicad_pcb]
2020-01-15 update schematic sheet name
    [kicad-eboard.sch]
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2020-01-29 Update inductor footprint, positioning
    [kicad-eboard.kicad_pcb]
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2020-02-01 Add separate SSR for power
    [MP6050.sch, kicad-eboard.sch]
2020-02-01 Rename potentiometer, add 3d model
    [kicad-eboard.sch]
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2020-02-01 Use Powerpole footprints, resistor arrays
    [kicad-eboard.sch]
2020-02-08 Update resistor, cap footprints
    [kicad-eboard.sch]
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2020-02-11 Rearrange for current sensing
    [kicad-eboard.sch]
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2020-02-11 Add current sense amps (not connected to anything)
    [kicad-eboard.sch]
2020-02-12 Redo INA4181, add MCP3008
    [MP6050.sch, kicad-eboard.sch]
2020-02-12 Add encoder, current filtering
    [MP6050.sch, kicad-eboard.sch]
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2020-02-13 Add some test points
    [kicad-eboard.sch]
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2020-02-17 Remove unused encoder PWM
    [kicad-eboard.sch]
2020-02-17 Add servo, decoupling caps
    [kicad-eboard.sch]
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2020-02-17 Separate analog/digital ground, Vref
    [kicad-eboard.sch]
2020-02-17 Fix INA4181 pin type
    [kicad-eboard.sch]
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2020-02-17 Change big cap footprint
    [kicad-eboard.sch]
2020-02-17 Add some example routing
    [kicad-eboard.kicad_pcb]
2020-02-17 Add capacitor array symbol
    [kicad-eboard.sch]
2020-02-17 Add capacitor array footprint
    [MP6050.sch, kicad-eboard.kicad_pcb, kicad-eboard.sch]
2020-02-18 Add Tinker Board outline
    [MP6050.sch, kicad-eboard.kicad_pcb, kicad-eboard.sch]
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2020-02-18 Tweaks, fix INA4181 bypass caps
    [kicad-eboard.kicad_pcb, kicad-eboard.sch]
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2020-02-20 Swap M1,m2 current sense
    [kicad-eboard.kicad_pcb, kicad-eboard.sch]
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2020-02-22 Fix Powerpole 3D/connection issue; more silkscreen
    [kicad-eboard.kicad_pcb, kicad-eboard.sch]
2020-02-22 Fix test point labels (oops)
    [kicad-eboard.kicad_pcb]
2020-02-22 Add logo symbols, standardize component values
    Added a hacky almost-invisible schematic symbol for graphics, because
    otherwise hitting "Update PCB from Schematic" will delete footprints
    that aren't in the schematic. Also standardized component values - prefer
    100n to 0.1u; prefer 100n to 100nF; prefer 100k to 100K.
    [MP6050.sch, kicad-eboard.kicad_pcb, kicad-eboard.sch]
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2020-02-24 Fix some unconnected nets
    [kicad-eboard.kicad_pcb]
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2020-09-17 Revert "added date"
    This reverts commit 0cdd8ac6e1c1616e55c703b4a8624dca90b81dce.
    [MP6050.sch, kicad-eboard.sch]
2021-11-08 Update README.md
    https://forum.kicad.info/t/warning-avoid-all-links-to-kicad-pcb-org-use-kicad-org/31521
